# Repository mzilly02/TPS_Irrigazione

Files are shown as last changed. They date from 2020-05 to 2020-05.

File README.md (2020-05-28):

# TPS_Irrigazione
Sistema di irrigazione con 5 aree programmabili e gestione attivazione tramite sensori di umidità industriali e sistema RTC DS1307 (Timer I2C).

Il progetto si basa su un Arduino Uno R3 incluso in un PCB custom (dimensioni nel file .brd), il tutto montato in un case stampato in 3d su una barra DIN (barra 35mm per montaggio PLC). 

L’intero sistema è inserito in una scatola di distribuzione impermeabile per permettere all’utente di installare il sistema di controllo all’esterno.

Il sistema è alimentato tramite un alimentatore per PLC a 12V / 2,5A MAX con doppia uscita 12V (Arduino e elettrovalvole).

Controllo del sistema tramite 4 tasti: SET, SW, UP e DOWN.

visualizzazione dati usando i display 7 segmenti in connessione I2C.

I sensori di umidità industriali sono attivati quando è presente una programmazione, per permettere un risparmio d'acqua all'utente.

L'attivazione dell'irrigazione è attuata tramite 5 elettrovalvole a 12v di tipo NC, controllate da 5 relè a stato solido.

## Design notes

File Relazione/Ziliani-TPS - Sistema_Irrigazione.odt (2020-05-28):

Indice della seguente relazione tecnica:

- Descrizione generale del progetto richiesto
- Schema elettrico
- Lista componenti di EAGLE
- Informazioni utili su alcuni componenti
- Specifiche del circuito stampato
- Descrizione del programma di gestione tramite flowchart (da SX a DX)
- Considerazioni su alcuni aspetti del programma di gestione

Descrizione generale del progetto richiesto:

Sistema di irrigazione con 5 aree programmabili e gestione attivazione tramite sensori di umidità industriali e sistema RTC DS1307 (Timer I2C).

Il progetto si basa su un Arduino Uno R3 incluso in un PCB custom (dimensioni nel file .brd), il tutto montato in un case stampato in 3d su una barra DIN (https://www.thingiverse.com/thing:3531692) (barra 35mm per montaggio PLC).

L’intero sistema è inserito in una scatola di distribuzione impermeabile (https://www.amazon.it/Cablematic-Scatola-distribuzione-elettrica-montaggio/dp/B00U9SOVA8?__mk_it_IT=ÅMÅŽÕÑ) per permettere all’utente di installare il sistema di controllo all’esterno.

Il sistema è alimentato tramite un alimentatore per PLC a 12V / 2,5A MAX (https://www.amazon.it/Auforua®-Alimentatore-Monofase-montaggio-approvato/dp/B06VV25ZR5) con doppia uscita 12V (Arduino e elettrovalvole).

Controllo del sistema tramite 4 tasti: SET, SW, UP e DOWN.

visualizzazione dati usando i display 7 segmenti in connessione I2C.

I sensori di umidità industriali sono attivati quando è presente una programmazione, per permettere un risparmio d'acqua all'utente.

L'attivazione dell'irrigazione è attuata tramite 5 elettrovalvole a 12v di tipo NC, controllate da 5 relè a stato solido.

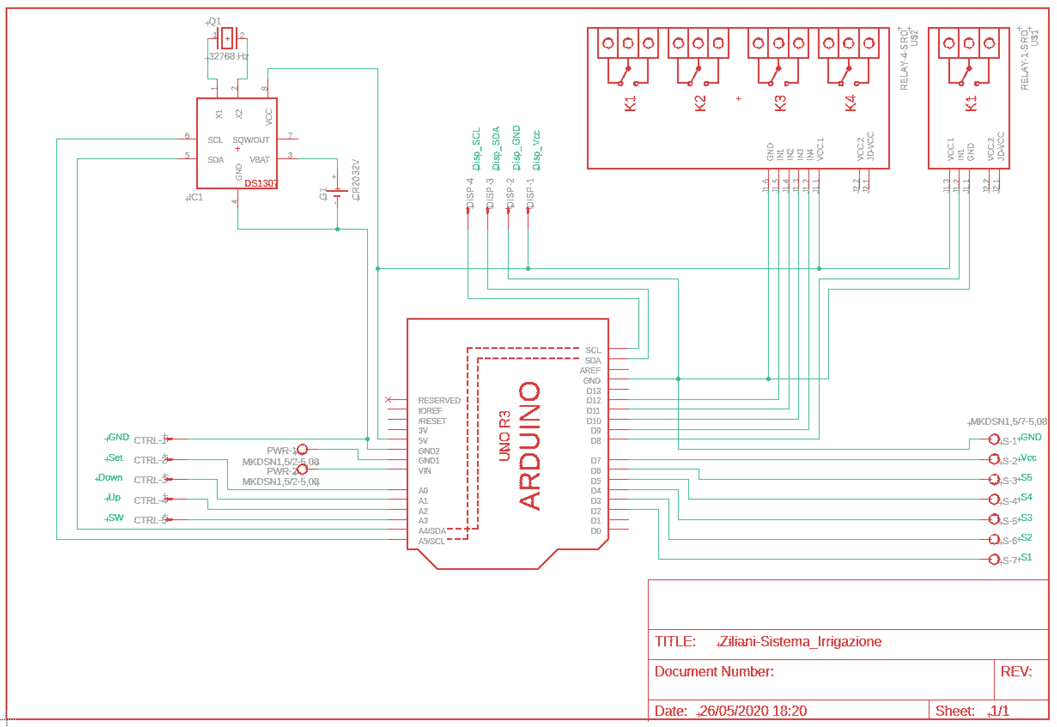
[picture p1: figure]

Schema elettrico:

Lista componenti di EAGLE:

Part | Value | Device | Package
CTRL | | L05P | L05P
DISP | | L04P | L04P
G1 | CR2032V | CR2032V | CR2032V
IC1 | DS1307 | DS1307 | DIL08
PWR | MKDSN1,5/2-5,08 | MKDSN1,5/2-5,08 | MKDSN1,5/2-5,08
Q1 | 32768 Hz | XTAL/S | QS
S | MKDSN1,5/7-5,08 | MKDSN1,5/7-5,08 | MKDSN1,5/7-5,08
U$1 | RELAY-1-SRD | RELAY-1-SRD | RELAY-1-SRD
U$2 | RELAY-4-SRD | RELAY-4-SRD | RELAY-4-SRD
U1 | ARDUINO UNO R3 | ARDUINO UNO R3 | ARDUINOR3

CTRL e DISP sono due connettori di tipo AMP MT: CTRL per il collegamento ad Arduino dei 4 tasti di controllo + GND e DISP per il collegamento con il display 4 cifre a 7 segmenti.

I componenti IC1, U$1, U$2 e U1 fanno parte delle librerie aggiuntive “adafruit-MOD” (IC1 e U1) e “diy-modules-PCB” (U$1 e U$2).

Le due librerie sono derivate dalle librerie “adafruit” e “diy-modules”, le modifiche sono state rese necessarie per ottenere: moduli relays senza il profilo sul PCB, profilo dell’Arduino Uno R3 compatibile con un piano di massa singolo.

Informazioni utili su alcuni componenti:

- I 4 tasti di controllo sono di tipo NA, nel codice di Arduino vengono inizializzati come INPUT_PULLUP.
- Il display 4 cifre a 7 segmenti è prodotto da Adafruit ed è un display con board integrata per la comunicazione tramite protocollo I2C. Il display è il seguente: Adafruit 4-digit 7 segment (https://www.adafruit.com/product/878).
- L’orologio RTC scelto è il DS1307 (datasheet (https://datasheets.maximintegrated.com/en/ds/DS1307.pdf)) perché permette una comunicazione tramite il protocollo I2C.
- La batteria tampone usata per alimentare l’RTC è una CR2032.
- I sensori di umidità del terreno sono di tipo professionale, con logica di controllo (comparatore LM393 (https://www.ti.com/lit/ds/symlink/lm393-n.pdf) e modifica del valore di soglia tramite trimmer) integrabile in vicinanza del sensore stesso, con opportune aggiunte. Il sensore è il seguente: ARCELI modulo sensore di umidità (https://www.amazon.it/ARCELI-sensore-rilevamento-Resistenza-corrosione/dp/B07RGJHQ1L).
- I moduli relè sono basati sui relè a stato solido della Handsontec: 1 Channel (https://handsontec.com/dataspecs/relay/1Ch-relay.pdf) e 4 Channel (https://www.handsontec.com/dataspecs/4Ch-relay.pdf).

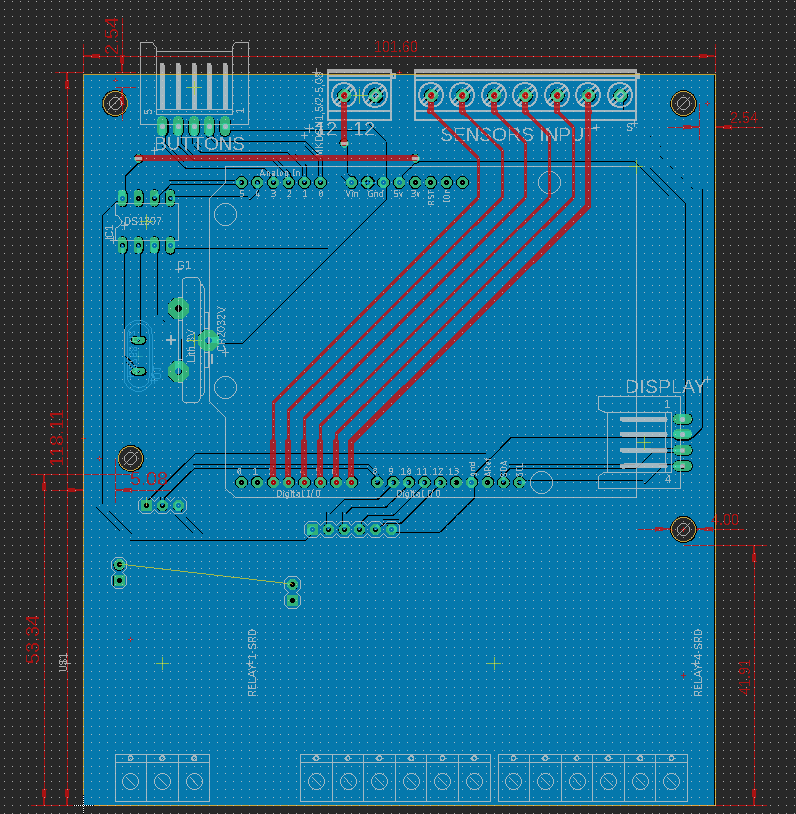
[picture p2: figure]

Specifiche del circuito stampato:

Il circuito stampato realizzato usando il programma Autodesk Eagle ha dimensioni di

101,60mm x 118,11mm, presenta 4 fori di montaggio.

I fori di montaggio hanno un diametro di 4mm e sono distanziati come nell’immagine, questa disposizione permette di non dover riprogettare i moduli relè.

Il circuito stampato presenta una realizzazione a doppia faccia.

Le piste di collegamento sono di due dimensioni diverse: 16mil (0,4mm) per i segnali e 32mil (0,8mm) per le alimentazioni.

Descrizione del programma di gestione tramite flowchart (da SX a DX):

Start: Setup:

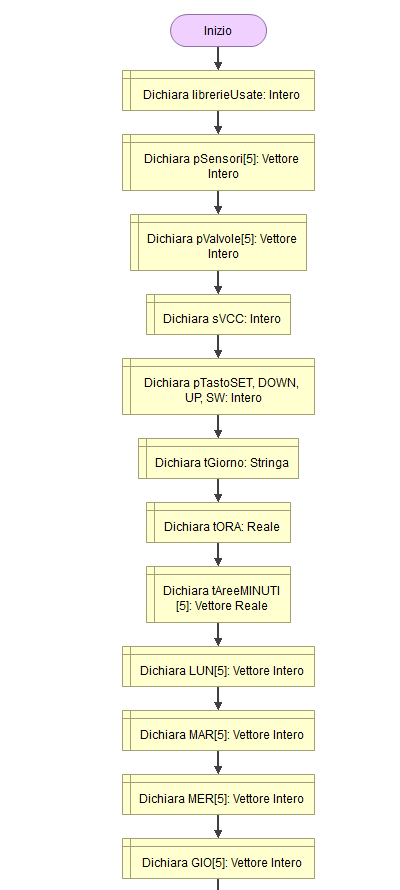
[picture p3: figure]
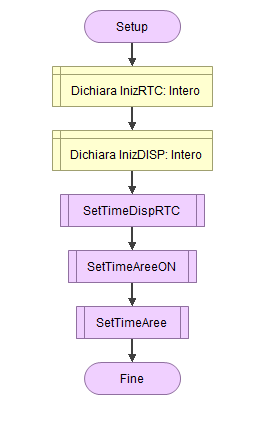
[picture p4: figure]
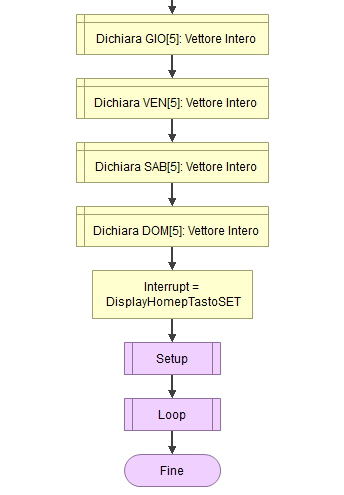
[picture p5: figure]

Descrizione del programma di gestione tramite flowchart (da SX a DX):

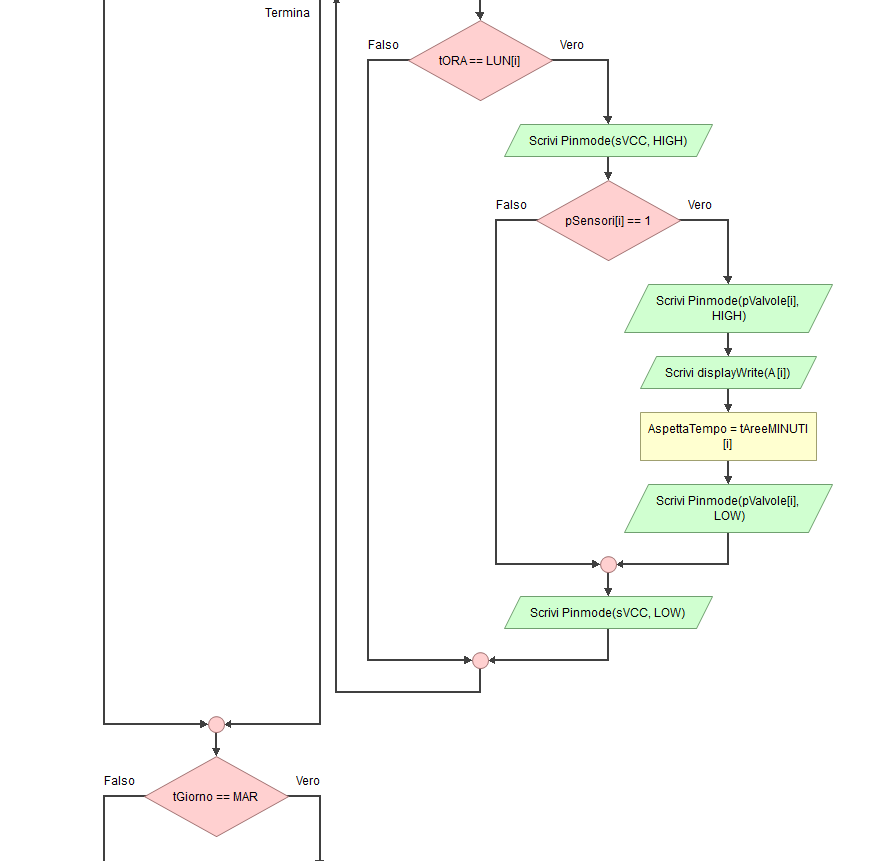
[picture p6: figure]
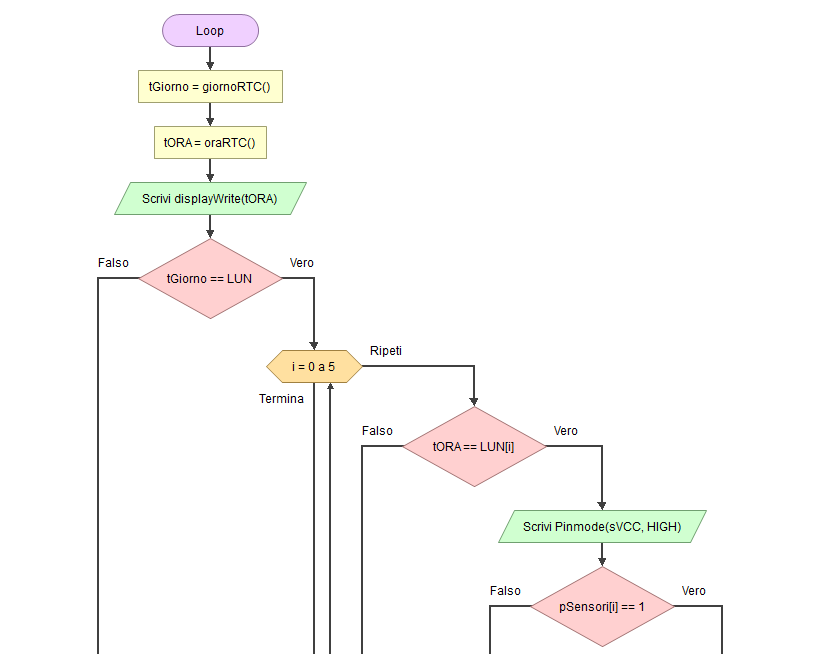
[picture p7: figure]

Loop:

Il test di tGiorno si ripete 7 volte, per controllare i giorni da Lunedì a Domenica, la struttura dei test si differenzia solamente per il giorno scansionato.

Descrizione del programma di gestione tramite flowchart (da SX a DX):

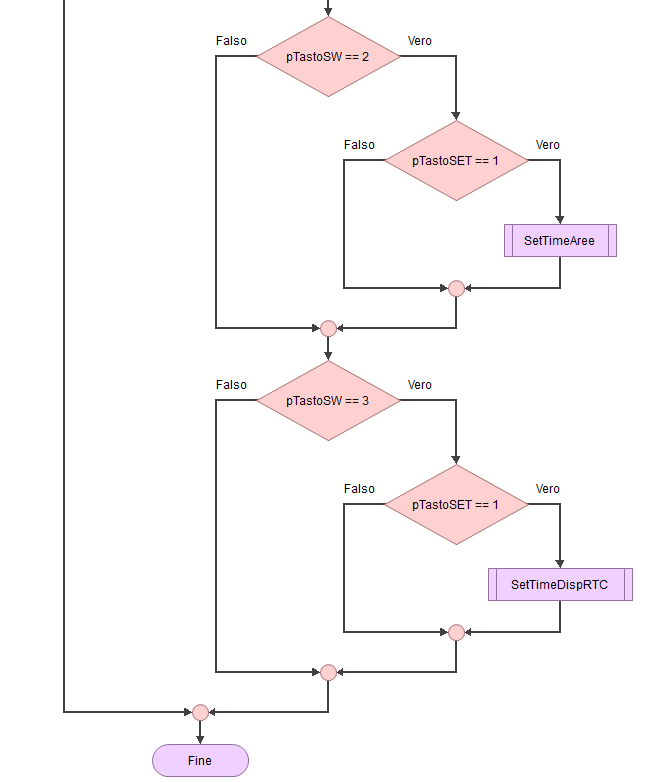
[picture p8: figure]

DisplayHome – Interrupt su tasto SET:

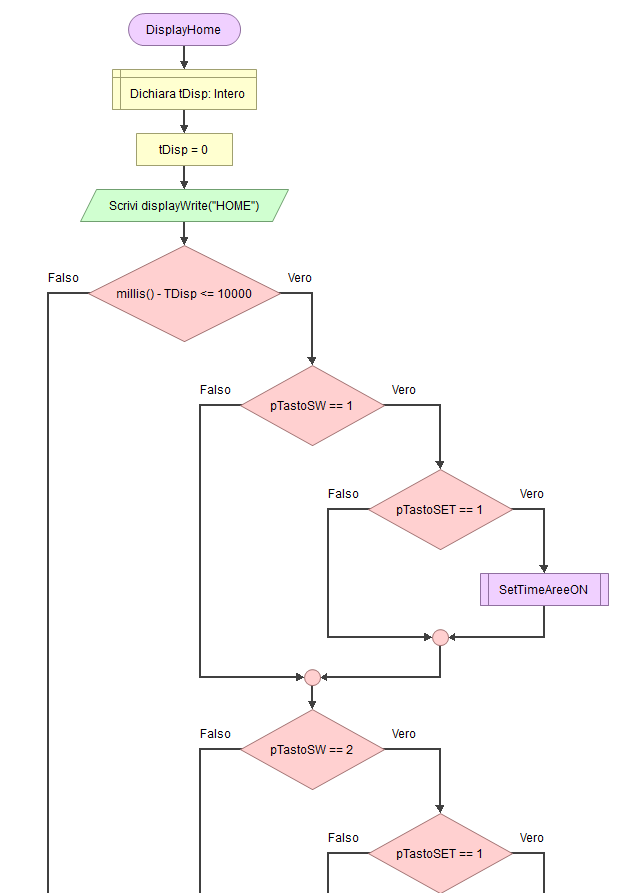
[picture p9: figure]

Descrizione del programma di gestione tramite flowchart (da SX a DX):

SetTimeDispRTC:

Permette all’utente di impostare l’ora e il giorno corrente e di salvarlo automaticamente nell’orologio RTC.

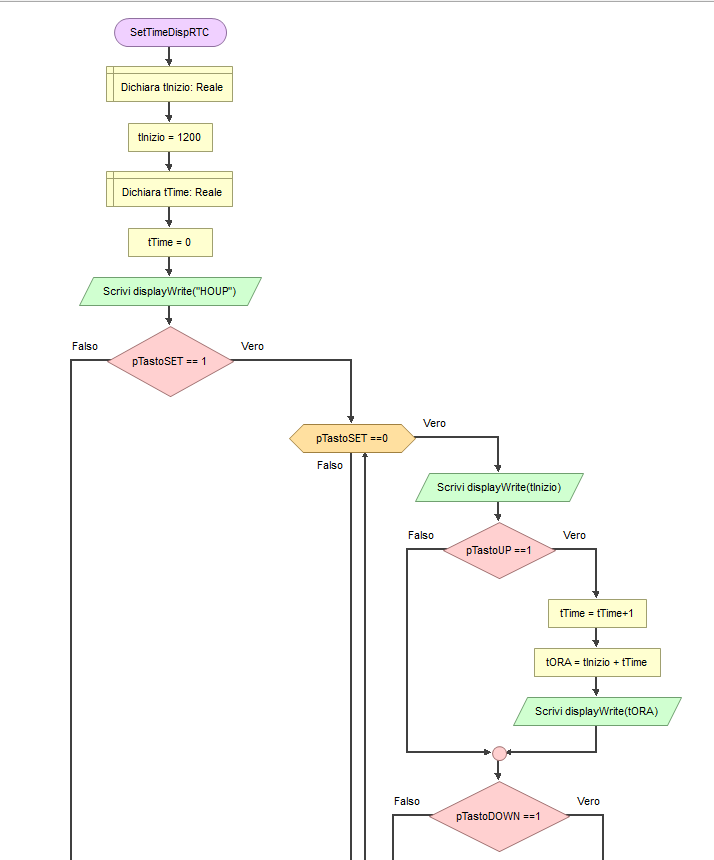
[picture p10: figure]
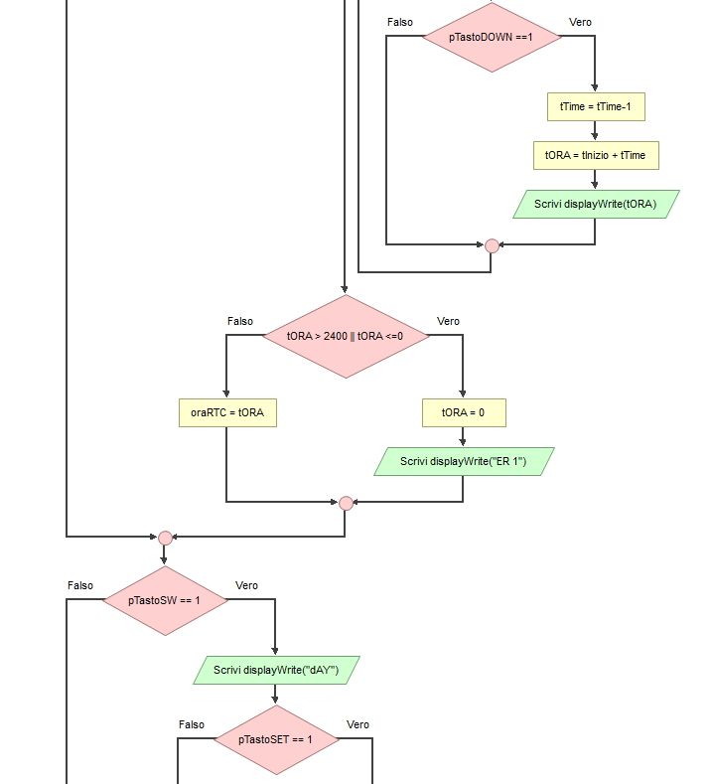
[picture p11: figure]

Descrizione del programma di gestione tramite flowchart (da SX a DX):

SetTimeDispRTC:

Permette all’utente di impostare l’ora e il giorno corrente e di salvarlo automaticamente nell’orologio RTC.

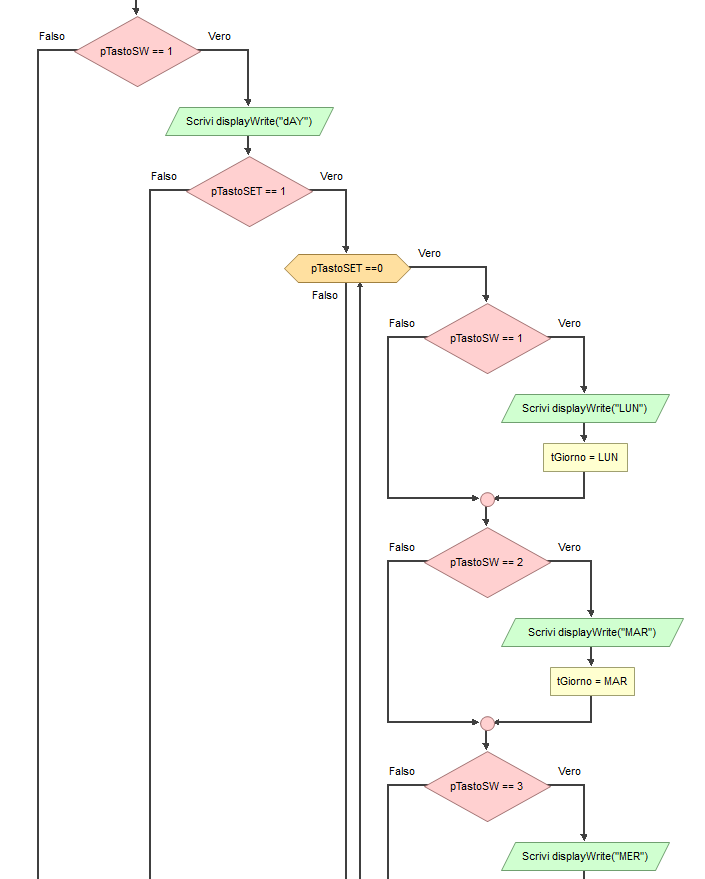
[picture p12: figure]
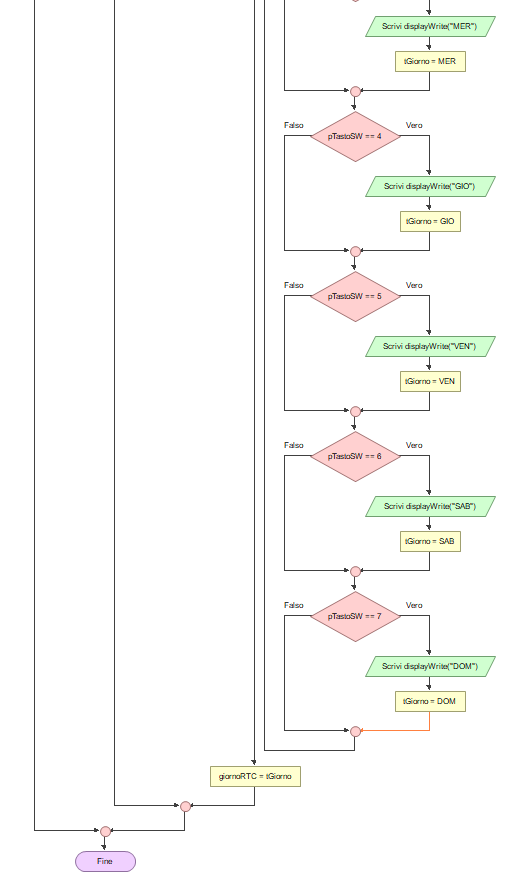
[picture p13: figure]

Descrizione del programma di gestione tramite flowchart (da SX a DX):

SetTimeAreeON: Permette di impostare i tempi di attivazione delle 5 aree (5 test con scrittura in vettore).

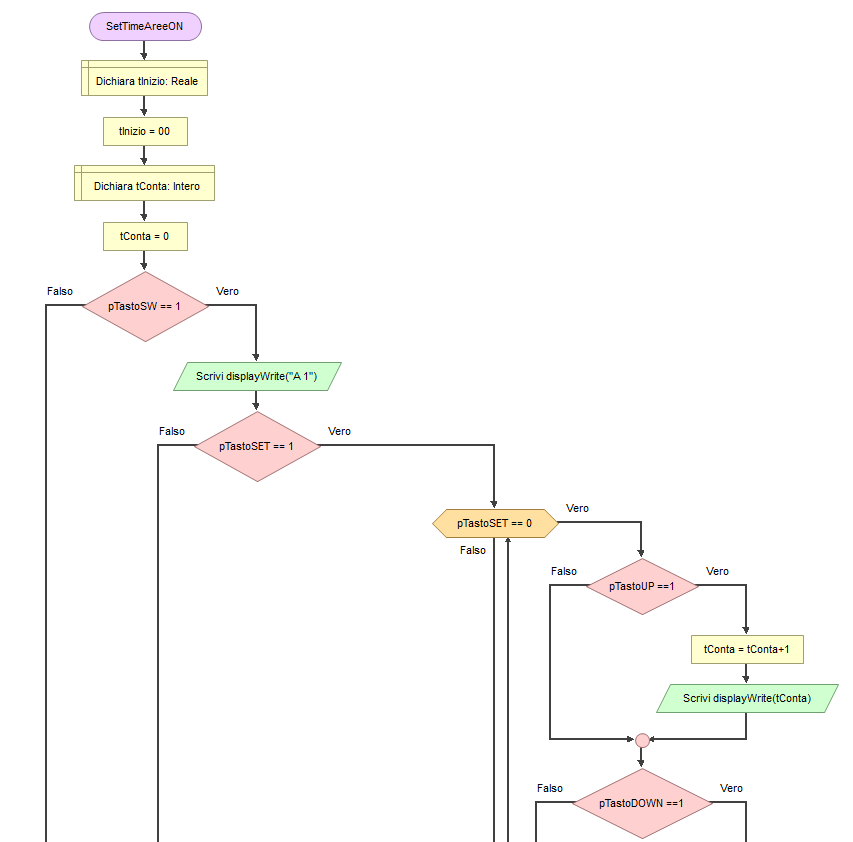
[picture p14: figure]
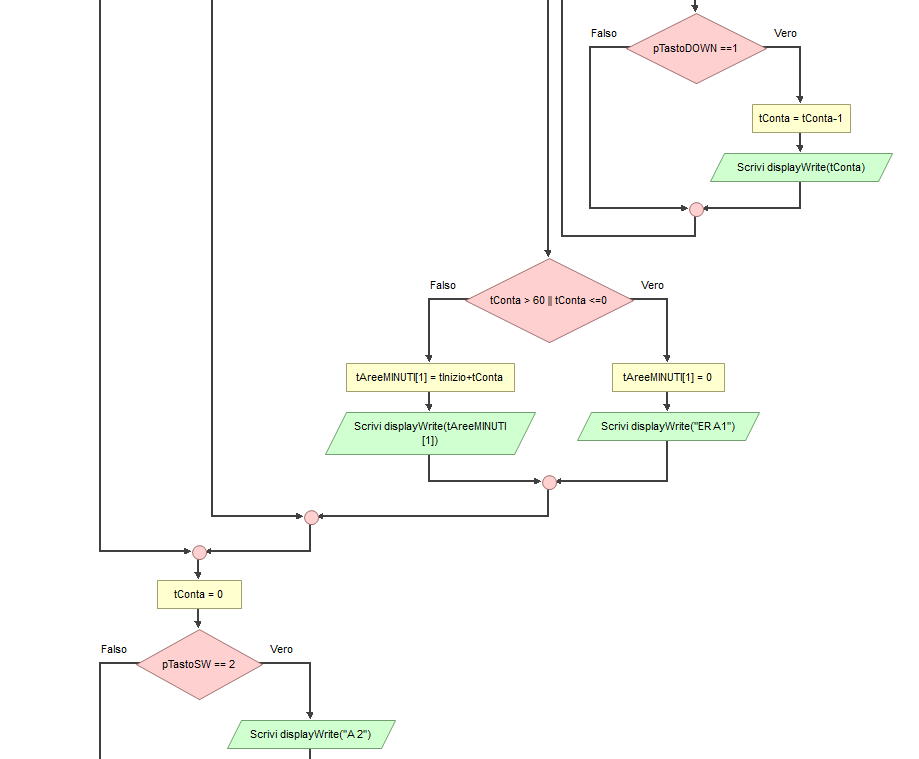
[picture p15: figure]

Descrizione del programma di gestione tramite flowchart (da SX a DX):

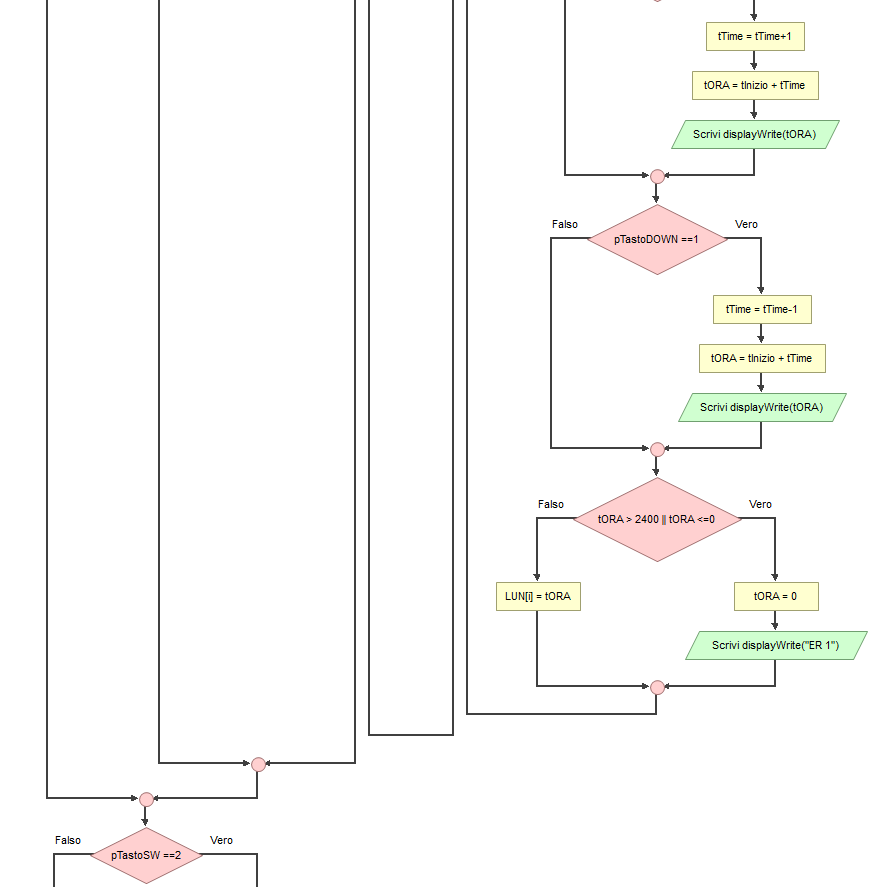
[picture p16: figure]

SetTimeAree: vengono eseguiti 7 test, in base al numero di pressioni del tasto SW, viene visualizzato il giorno della settimana e richiesta l’ora di attivazione.

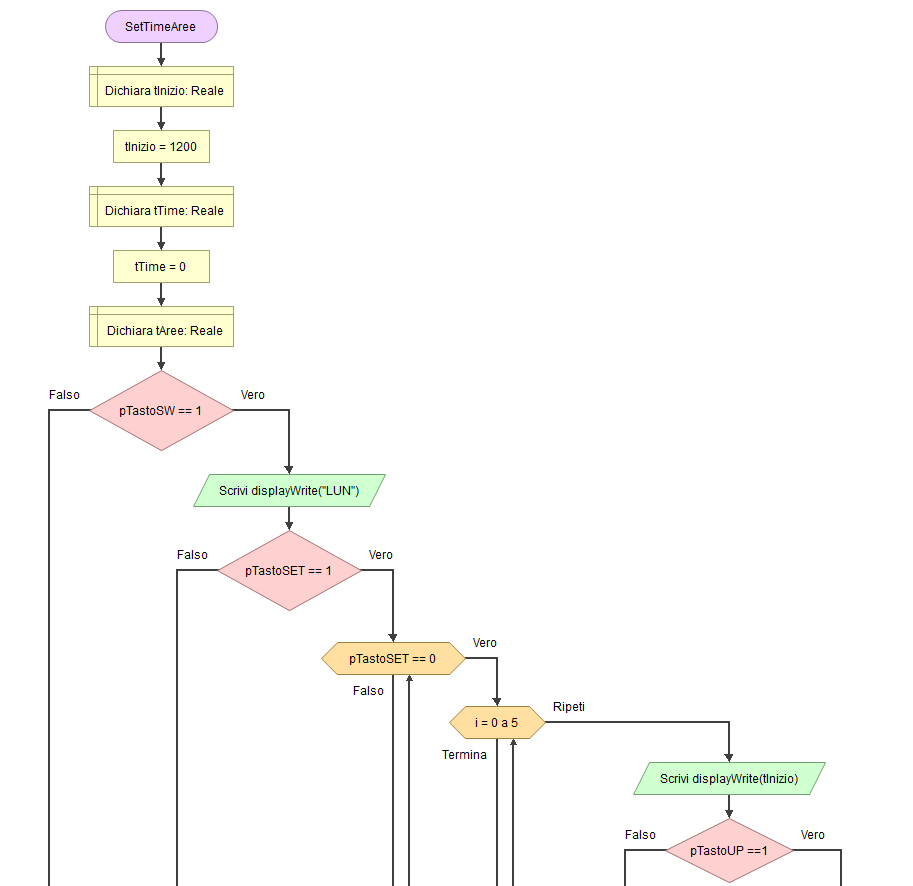
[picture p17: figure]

Considerazioni su alcuni aspetti del programma di gestione:

Il file del flowchart è stato creato con il programma Flowgorithm. Il file è disponibile su Github qui (https://github.com/mzilly02/TPS_Irrigazione/tree/master/Flowchart).

Il vettore pSensori [5] contiene i dati che corrispondono ai pin dei sensori; Il vettore è inizializzato con i seguenti pin:

[2, 3, 4, 5, 6] .

sVCC corrisponde al pin di alimentazione dei sensori, il pin 7 .

Il vettore pValvole [5] contiene i dati che corrispondono ai pin per attivare i relè; Il vettore è inizializzato con i seguenti pin: [8, 9, 10, 11, 12] .

I pin pTastoSET, pTastoDOWN, pTastoUP e pTastoSW sono i seguenti: A0, A1, A2, A3 .

L’utente, una volta acceso il sistema e definito per la prima volta l’ora corrente e il giorno corrente (SetTimeDispRTC) e le opzioni della programmazione (SetTimeAreeON, permette di scegliere i tempi di attivazione delle 5 aree fino ad un massimo di 60 minuti; SetTimeAree, permette di selezionare per i 7 giorni gli orari di attivazione delle aree), può modificare in qualsiasi momento le programmazioni delle aree e l’ora corrente.

Per entrare nel menù, premere in qualsiasi momento il tasto SET, successivamente premere il tasto SW per selezionare l’opzione desiderata:

1 click = Imposta tempi attivazione aree, 2 click = imposta giorni e ore di attivazione, 3 click = impostare l’ora corrente. Per entrare nei 3 menù, una volta scelto con SW, premere SET.

In caso che l’utente non esegua nessuna scelta in un tempo di 10 secondi, il sistema ritorna automaticamente a visualizzare l’ora corrente.

Ad ogni avvio successivo ad una perdita di corrente, il sistema richiede di impostare l’ora, questo per evitare che l’orologio RTC possa calcolare un ora sbagliata.

Sistema di irrigazione automatizzato – Progetto di Mattia Ziliani

Torna all’indice Pagina 14

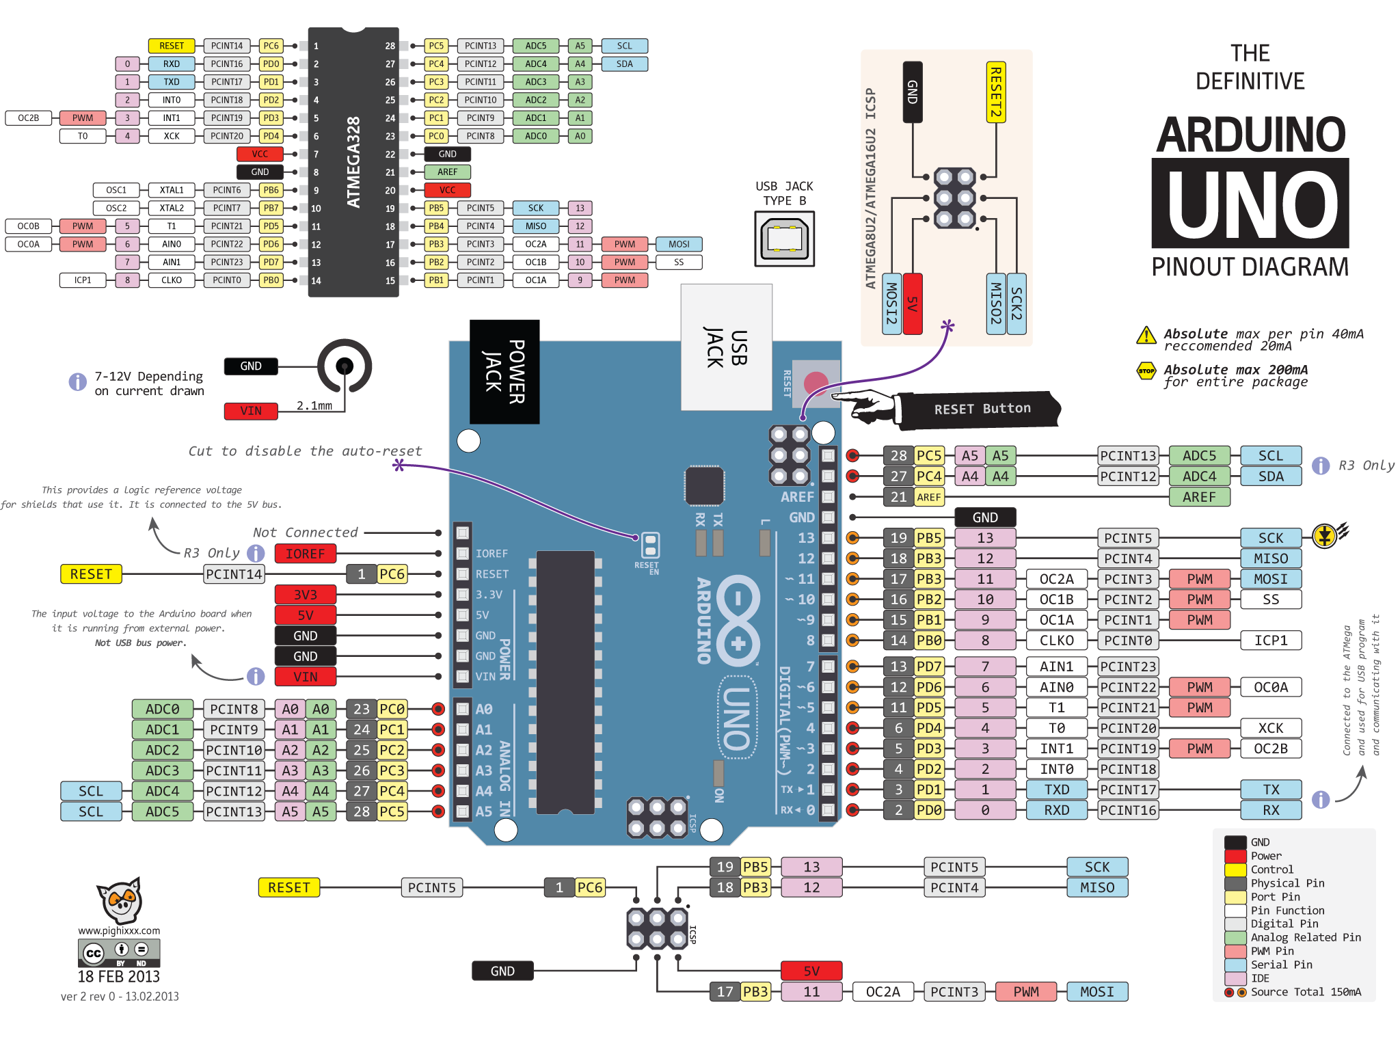
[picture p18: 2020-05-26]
Datasheet/Arduino_UNO.png

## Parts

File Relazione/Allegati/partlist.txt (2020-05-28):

Partlist

Exported from Ziliani-Sistema_Irrigazione.sch at 25/05/2020 19:26

EAGLE Version 9.6.1 Copyright (c) 1988-2020 Autodesk, Inc.

Assembly variant: 

Part     Value               Device              Package         Library         Sheet

CTRL                         L05P                L05P            con-amp-mt      1
DISP                         L04P                L04P            con-amp-mt      1
G1       CR2032V             CR2032V             CR2032V         battery         1
IC1      DS1307              DS1307              DIL08           adafruit        1
PWR      MKDSN1,5/2-5,08     MKDSN1,5/2-5,08     MKDSN1,5/2-5,08 con-phoenix-508 1
Q1       32768 Hz            XTAL/S              QS              special         1
S        MKDSN1,5/7-5,08     MKDSN1,5/7-5,08     MKDSN1,5/7-5,08 con-phoenix-508 1
U$1      RELAY-1-SRD         RELAY-1-SRD         RELAY-1-SRD     diy-modules-PCB 1
U$2      RELAY-4-SRD         RELAY-4-SRD         RELAY-4-SRD     diy-modules-PCB 1
U1       ARDUINOR3-DIMENSION ARDUINOR3-DIMENSION ARDUINOR3       adafruit-MOD    1

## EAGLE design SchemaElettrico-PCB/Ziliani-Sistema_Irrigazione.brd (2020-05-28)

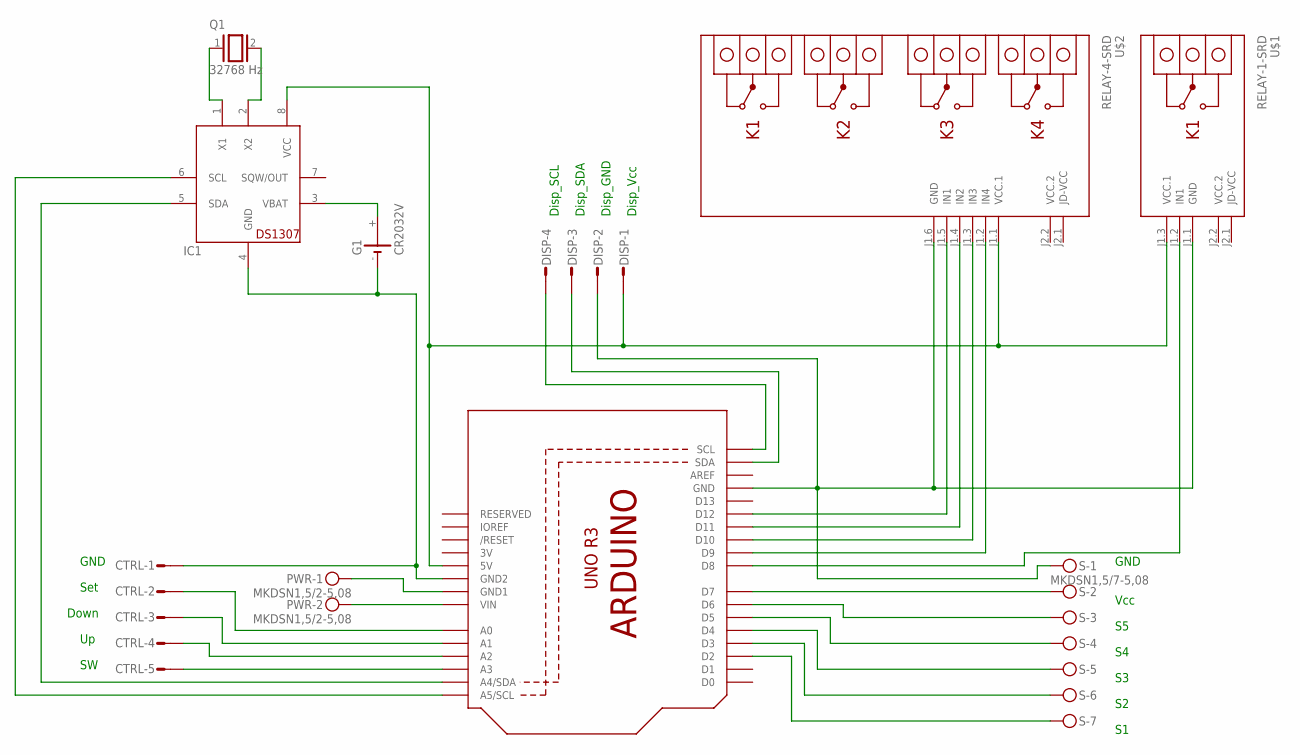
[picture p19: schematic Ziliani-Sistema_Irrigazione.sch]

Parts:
CTRL: L05P
DISP: L04P
G1: CR2032V
IC1: DS1307; DIL08
PWR: MKDSN1,5/2-5,08
Q1: 32768 Hz; QS
S: MKDSN1,5/7-5,08
U1: ARDUINOR3-DIMENSION; ARDUINOR3
U$1: RELAY-1-SRD
U$2: RELAY-4-SRD

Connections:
3V: U1.3V
GND: PWR.1, U1.GND1
unnamed: G1.+, IC1.3 (VBAT)
unnamed: DISP.4, U1.SCL
unnamed: IC1.2 (X2), Q1.2
unnamed: IC1.1 (X1), Q1.1
unnamed: CTRL.2, U1.A0
unnamed: IC1.5 (SDA), U1.A4 (A4/SDA)
unnamed: IC1.6 (SCL), U1.A5 (A5/SCL)
unnamed: CTRL.1, G1.-, IC1.4 (GND), U1.GND2
unnamed: CTRL.3, U1.A1
unnamed: CTRL.4, U1.A2
unnamed: CTRL.5, U1.A3
unnamed: PWR.2, U1.VIN
unnamed: DISP.1, IC1.8 (VCC), U1.5V, U$1.J1.3 (VCC.1), U$2.J1.1 (VCC.1)
unnamed: U1.D11, U$2.J1.4 (IN2)
unnamed: DISP.2, S.1, U1.GND, U$1.J1.1 (GND), U$2.J1.6 (GND)
unnamed: S.7, U1.D2
unnamed: S.6, U1.D3
unnamed: S.5, U1.D4
unnamed: S.4, U1.D5
unnamed: S.3, U1.D6
unnamed: S.2, U1.D7
unnamed: DISP.3, U1.SDA
unnamed: U1.D8, U$1.J1.2 (IN1)
unnamed: U1.D10, U$2.J1.3 (IN3)
unnamed: U1.D9, U$2.J1.2 (IN4)
unnamed: U1.D12, U$2.J1.5 (IN1)
VCC.2: U$1.J2.2 (VCC.2), U$2.J2.2 (VCC.2)

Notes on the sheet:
GND
Down
Set
Vcc
Disp_Vcc
Disp_GND
Disp_SDA
Disp_SCL

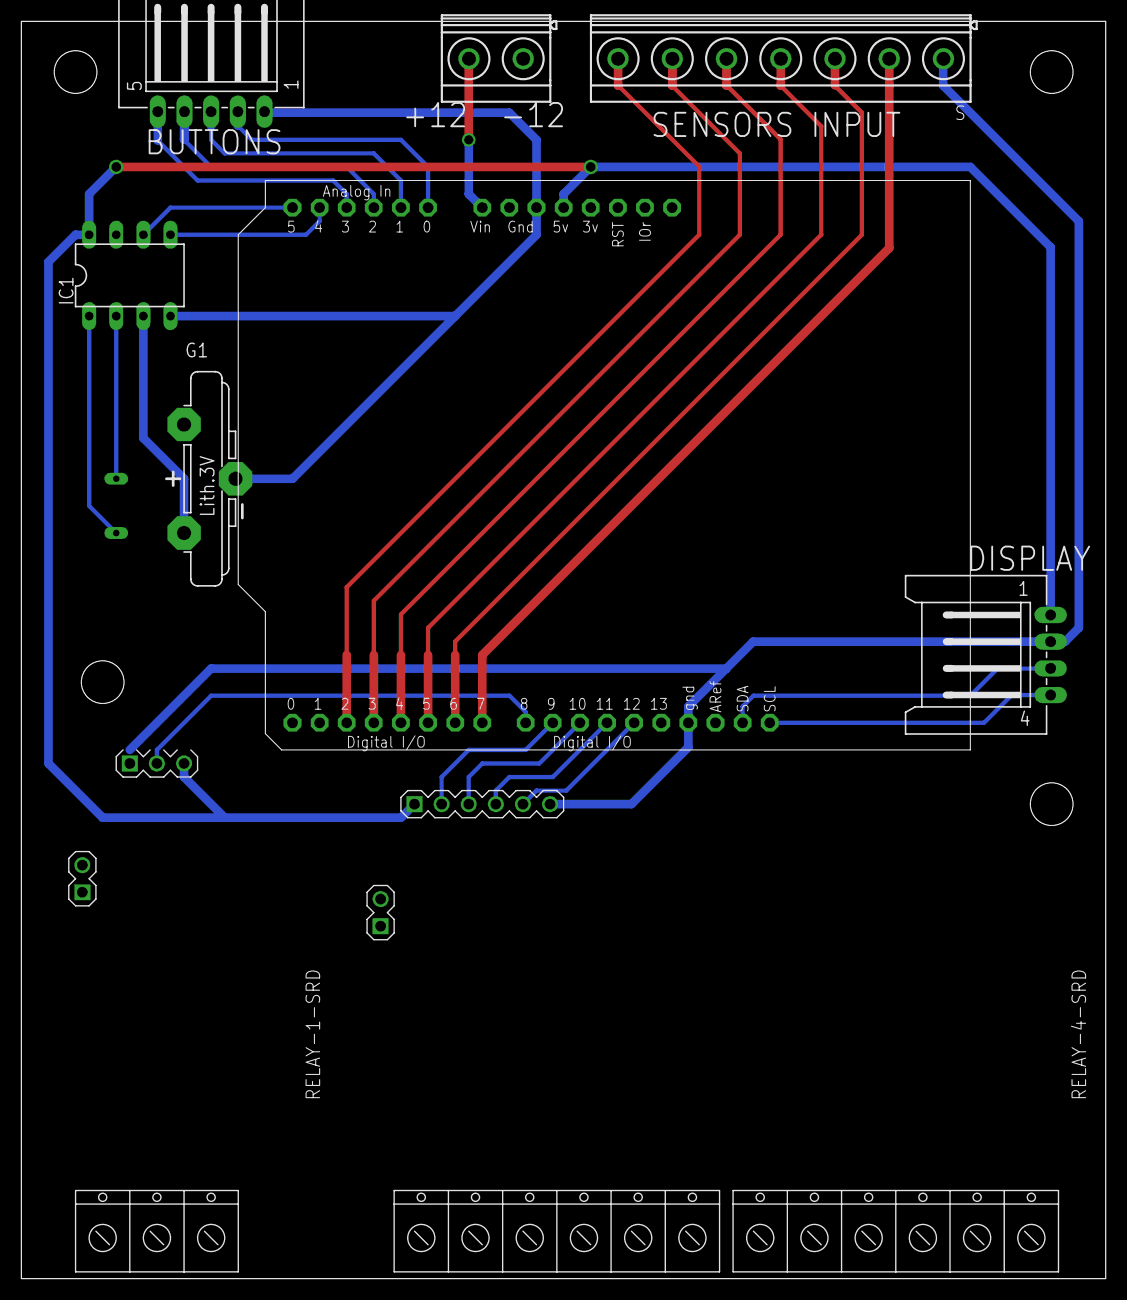
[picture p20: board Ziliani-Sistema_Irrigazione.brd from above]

Board: 2 copper layers, 101.6 x 117.8 mm, 10 parts (1 on the bottom side), 28 nets.

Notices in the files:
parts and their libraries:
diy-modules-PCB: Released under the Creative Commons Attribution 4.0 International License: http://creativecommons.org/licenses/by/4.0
